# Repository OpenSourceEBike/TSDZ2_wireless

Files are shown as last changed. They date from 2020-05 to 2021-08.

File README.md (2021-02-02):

NEW UPDATED DOCUMENTATION HERE: https://opensourceebike.github.io/

https://opensourceebike.github.io/

# TSDZ2 Wireless

- Forum message: [Fully wireless ANT+ BLE TSDZ2 mid drive motor (like Specialized Turbo Levo) -- Flexible OpenSource firmware](https://endless-sphere.com/forums/viewtopic.php?t=106346)
- Developers: see [documentation](documentation/README.md)

We are also developing our own wireless remote although any other comercial wireless EBike remote will work: https://github.com/OpenSource-EBike-firmware/ebike_wireless_remote

TSDZ2 Wireless project aims
------------

This project aims to make TSDZ2 mid drive motor support wireless displays and wireless remote control buttons just like the new commercial ebikes as [Specialized Turbo Levo Ebike](https://www.youtube.com/watch?v=F43oqj1Zlww).

A very simple and cheap DIY board, that costs only 25€, will implement the wireless ANT+ LEV and Bluetooth. This board can be placed inside a small and waterproof black box, that will connect to the TSDZ2 motor display connector.

The wireless displays and wireless remote buttons are available from some different brands: Garmin, Wahoo, Sigma, O-synce, Specialized and Selfloops. Somes displays are simple with a monochrome screen and others are very advanced with GPS navigation, cycling fitness metrics and with wireless connection to cycling sensors like pedal power sensors and even tire pressure sensors.

The LCD Display will be replaced by the DIY board, a nRF52840 Bluetooth/ANT+ module and supporting circuitry. This allows the use of wireless buttons to control the TSDZ2 motor and it acts as a bridge between the motor, an Android phone running an app, and/or an ANT+ GPS/Fitness Display. It aims to be compatible with any display that can handle the ANT+ eBike data format, displaying relevant motor data and warnings. The Android app aims to duplicate (more or less) the 850C display, working either from the touchscreen or via wireless buttons on the handlebar.

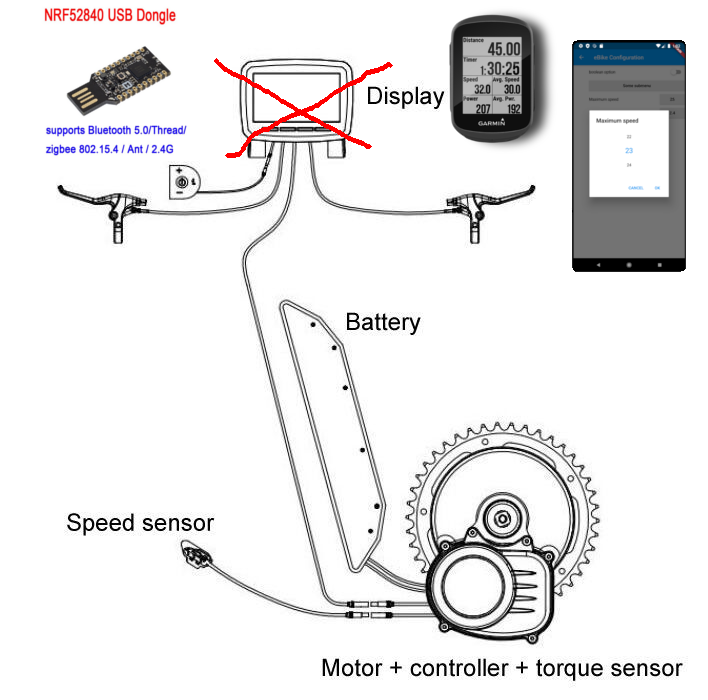
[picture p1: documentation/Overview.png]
Overview of connection


Warnings!
---------

1) Battery Voltage MUST!!!!!! be less than 60V otherwise smoke may escape.....
2) Spec. of DC-DC converter must be Input >60V and Output = 5V
3) Check output voltage of DC-DC converter BEFORE WIRING IT UP!!!

TSDZ2 cable pinout for LCD Display
----------------------------------
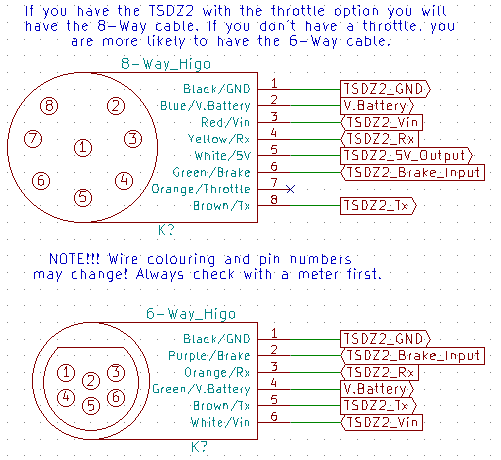
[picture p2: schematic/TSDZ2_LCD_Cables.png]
TSDZ2 Pinout for cables to standard LCD


The nRF52840 module needs to connect to the TSDZ2 motor-controller and the easiest way to do this is by either using an old LCD cable or buying an extension cable and cutting the relevant end off. The type of cable you have/need will depend on which TSDZ2 model you ordered - there are currently two types, one with a throttle and one without. The throttle needs a 5V connection as well as an anlogue input going to the motor-controller, so it has two extra cable - eight compared to the other motor-controller's six. For this project it is advised that you do not use the throttle, so either model is fine. The pinout of the two cable types is shown above - please note that the wire colouring and pin numbers may change! Always check with a meter first.

Connecting the nRF52840 UART to the TSDZ2 STM8S105 Motor-Controller UART
-------------------------------------------------------------------------------
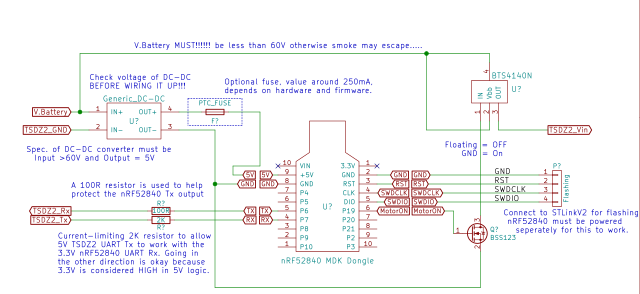
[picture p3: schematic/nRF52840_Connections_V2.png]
nRF52840 connections to peripherals


The TSDZ2 motor-controller's STM8S105 processor runs at 5V logic supply, whilst the nRF52840 processor runs at 3.3V. Unfortunately the nRF52 does not have 5V-tolerant GPIO inputs, so we need to be careful how we connect the two.

The nRF52 UART HIGH output (V.OH) is ~3.3V, which falls slightly out of the spec for the STM8S105 CMOS UART input, the datasheet for which states that 0.7xV.DD (3.5V) is expected for V.IH when run at 5V. However in practice it works reliably. So, as per the various 3.3V LCD displays, we can connect the nRF52 UART 3.3V output directly to the STM8S105 UART input, as shown above. For additional ESD safety we can add an optional low-value resistor to the nRF52 UART output.

Connecting the 5V STM8S105 UART output to the 3.3V nRF52 UART input is more problematic and there are [an almost infinite number of ways of doing this](https://next-hack.com/index.php/2017/09/15/how-to-interface-a-5v-output-to-a-3-3v-input/ "a random guide to interfacing 5v to 3.3v logic"). The easiest way is to rely on the [nRF52's input protection diodes](io_protection.png) to keep the input voltage below the maximum allowed.

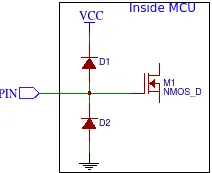
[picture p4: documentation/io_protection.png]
nRF52840 input protection diodes


If you just connect the two together a large amount of current will flow through the upper diode into the power supply, burning the diode out almost instantly and then destroying the input circuitry as the maximum voltage is exceeded. To avoid this, a current-limiting resistor is used as shown above. __NOTE__ - there is a trade off between small-resistor/high-current/high-speed and large-resistor/low-current/low-speed.

The absolute best way would be to use a pair of buffer/translators, [one with a TTL input running at 5V](https://www.ti.com/product/SN74AHCT1G125 "something similar to this") to drive the STM8S105 UART's input with a low-impedance output, and the other [with a CMOS input running at 3.3V](https://www.ti.com/product/SN74LVC1G34 "and something like this") to offer a high-impedance 5V-tolerant input to the STM8S105 UART's output. This offers the optimum noise resistance but at a higher cost and component count.

Connecting the nRF52840 to the STLinkV2 Programmer
--------------------------------------------------
For convenience it is advised that you permanently wire in a connector to allow programming the nRF52840, to allow for future Firmware updates - the pinout is up to you, as long as it matches the programmer's cable. Please note that the nRF52840 will need to be powered separately for the programming to be successful.

Connecting the nRF52840 to the BTS4140N High-Side Mosfet Relay
--------------------------------------------------------------
The high-side mosfet-relay input needs to be driven by an open-drain/open-collector circuit that can withstand the battery voltage across it when the device is floating. Following the BTS4140N datasheet on page 6, a BSS138 mosfet (supersedes BSS100) pulls the BTS4140N input to ground to make it conduct. When the mosfet is off, the BTS4140N stops conducting and the input floats at the battery voltage, which means that the Drain-Source breakdown voltage must be higher than 60V - the BSS138 is 100V.

Connecting power to the nRF52840
-------------------------------

A generic DC-DC converter is used to power the nRF52840's 5V input from the battery voltage. As such is should handle an input range of between 20V and 60V (check the capacitor ratings on the PCB) and provide a stable 5V supply at 1A. As mentioned above, connect it temporarily to your battery and check/adjust the output is correct before you start wiring up the nRF52840. When everything is connected up and running, it is worth checking it again and if it is adjustable, gluing the adjuster in place with a drop of nail-varnish - this has the right consistency to secure it against vibration but is easy enough to break the seal if you need to adjust it in the future. You can use a PTC fuse if you want - 250mA to 500mA is probably enough. Check it doesn't get warm/hot to the touch when in normal use - if it does, see how much voltage is being dropped across it and replace it with a larger value if it's more than 0.5Vish.
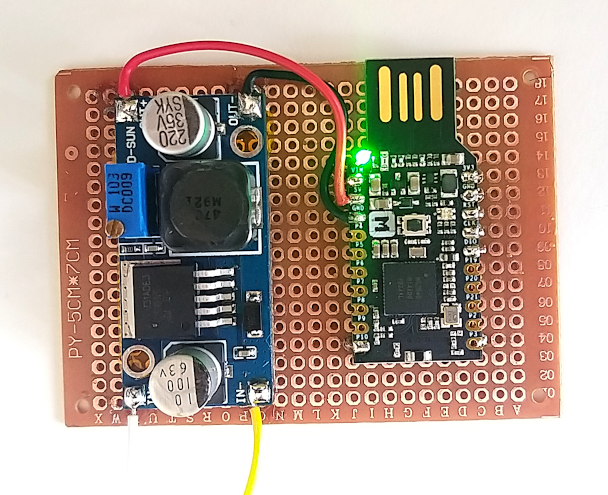
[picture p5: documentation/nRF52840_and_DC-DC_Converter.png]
Powering the nRF52840 with a DC-DC converter


Connecting brake sensors to the TSDZ2
-------------------------------------

It is strongly advised that you connect brake sensors/switches to the TSDZ2 motor-controller as it will increase safety of operation and reduce the chance of damage to the blue gear, in some circumstances. The brake input to the TSDZ2 is pulled up to 5V by a resistor inside the motor-controller, pulling the brake input to GND indicates that the brakes are being used. This is normally done with a switch (2-Pin Connector), but if you have the 8-Way Higo cable you can use a powered brake-sensor with three wires. In both cases the sensors need to be connected in parallel to the single TSDZ2 motor-controller brake input - check that any active sensors used have an open-collector output and are designed to be connected in parallel like this. The pinout and colour of the wires is likely to change without notice, so check first. An optional diode is shown, to protect from high voltages going into brake input. Use a Schottky type to reduce the dropped voltage when it's conducting. The optional Fuse is a PTC self-resetting type to protect the TSDZ2 5V supply - 50mA should be about right, but check the spec. of your 3-wire brake sensors first.

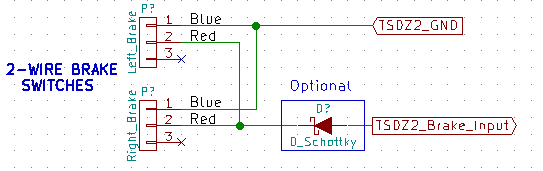
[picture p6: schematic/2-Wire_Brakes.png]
2-Wire brake connection


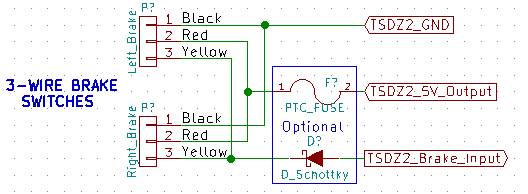
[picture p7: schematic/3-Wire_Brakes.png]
3-Wire brake connection


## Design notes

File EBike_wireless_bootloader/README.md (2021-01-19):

# TSDZ2 Bluetooth Bootloader

- Discussion Forum:[Fully wireless ANT+ BLE TSDZ2 mid drive motor (like Specialized Turbo Levo) -- Flexible OpenSource firmware](https://endless-sphere.com/forums/viewtopic.php?t=106346)
- Developers, see the [documentation](documentation/README.md)
- [We have also developed a wireless ebike controller for the TSDZ2 motor](https://github.com/OpenSource-EBike-firmware/TSDZ2_wireless)
as well as a [wireless remote control](https://github.com/OpenSource-EBike-firmware/ebike_wireless_remote); both use this bootloader.

-------
## Overview
This project implements a secure wireless bluetooth DFU bootloader for the TSDZ2 ebike remote control and motor controller. Once loaded on the Nordic Nrf52840 dongle, the firmware for both the remote and the wireless controller can be installed using bluetooth.

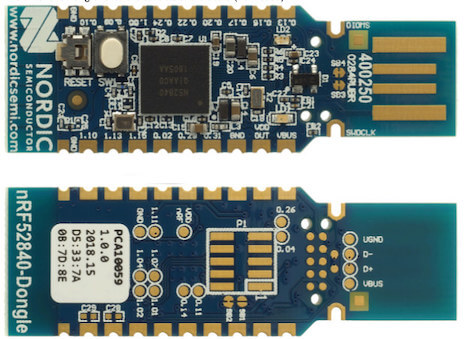
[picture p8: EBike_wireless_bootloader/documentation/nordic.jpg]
dongle


----
[Installing the Bootloader on the Nordic USB Dongle](documentation/getting_started.md)
-------
-------
[Loading New Firmware using the bootloader (the DFU Process)](documentation/dfu.md)
-----------
------------

[Technical Description](documentation/operation.md)
-----------
------------
[Security Encryption](documentation/configuration.md)
---------
---------
[Building the Bootloader](documentation/flashing.md)
------
------
[Bootloader Memory Map](documentation/memory_map.md)
-------
-------
[Important Note for Developers ](documentation/voltage_issue.md)
-------
-------
## Questions/Comments?
Please post on [this forum message](https://endless-sphere.com/forums/viewtopic.php?f=28&t=106346).

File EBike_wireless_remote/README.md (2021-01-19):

# EBike Handlebar Remote Controller

- Discussion Forum:[Fully wireless ANT+ BLE TSDZ2 mid drive motor (like Specialized Turbo Levo) -- Flexible OpenSource firmware](https://endless-sphere.com/forums/viewtopic.php?t=106346)
- Developers, see the [documentation](documentation/README.md)
- [We have also developed a wireless ebike controller for the TSDZ2 motor](https://github.com/OpenSource-EBike-firmware/TSDZ2_wireless)
as well as a [bootloader to be used with both the remote control and the ebike wireless controller](https://github.com/OpenSource-EBike-firmware/TSDZ2_wireless-bootloader)
## Overview
This project implements a wireless remote button for EBikes and/or GPS bike computers like the Garmin Edge. 
You can  purchase on the market ebike remote controls. ie: the [Garmin EBike Remote for about 80€](https://buy.garmin.com/en-US/US/p/545795/pn/010-12094-30).

However, our remote control is considerably less expensive and offers sevaral additional features for ebike control.

----
[Getting Started](documentation/getting_started.md)
-------
-------
[Operation](documentation/operation.md)
-----------
---
[ANT+ Control](documentation/features.md)
------------
------------
[Configuration Options](documentation/configuration.md)
---------
---------
[Battery considerations](documentation/battery.md)
-----
-----
[Further Development and Planned features](documentation/planned.md)
------
------

## Questions/Comments?
Please post on [this forum message](https://endless-sphere.com/forums/viewtopic.php?f=28&t=106346).

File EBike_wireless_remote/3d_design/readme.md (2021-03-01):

For 3D printing, use the files lower_part.stl and keypad.stl. Note that lower_part.stl seems to have non-manifold edges but I generated the GCode on Cura software and it printed well as if non-manifold edges are not an issue.

The other files are the sources files for the design on the FreeCAD 0.19 dev version. The assembly file has the assembly of the parts, including the NRF52 wireless board and the battery.

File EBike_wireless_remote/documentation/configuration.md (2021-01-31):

# Remote Configuration Options
The device configuration of the remote can be set via a bluetooth characteristic.

Once set, the configuration options are permanently stored in flash memory.
To change the remote configuration, long press the PLUS button to turn on bluetooth.
As an example of making a configuration change, see changing the ANT+ LEV Device Number (to connect to only one specific eBike) using the Nordic nRF Connect app in this video:

video (https://youtu.be/_ALauuDxZuQ) 

## The currently implemented configuration options are:
1. Setting the ANT+ Device number for the ANT LEV ebike. This ensures the remote will only pair to a specific ebike. valid inputs are hexadecimal 0x01 - 0x59 (decimal 01-89)
Please note that setting the device number to 0x00 is a 'wild card' setting that will cause the remote to pair with ANY ebike device number.
-----------------
2. __Turn on/off ANT+ LEV control.__ 
 (input hex 0x90 to turn on, hex 0x91 to turn off) 
This allows the remote to control only a garmin bike computer or any other device that implement the ANT+ Controls profile
----------
3. __Turn on/off ANT+ CONTROLS__  
 (input hex 0x92 to turn on, hex 0x93 to turn off)  
 This allows the remote to turn on/off the ANT+ CONTROLS capability depending on the use case. ie: the user may not have a garmin bike computer that needs to be controlled.
 --------
 4. __Turn on/off brake control__  depending on the use case
 (input hex 0x94 to turn on, hex 0x95 to turn off)  
 ---------
1. __Boot the remote control into Device Firmware Update (DFU) mode__ by inputting 0x99 to allow the remote firrmware to be updated wirelessly using bluetooth.
(input hex 0x99 to boot into DFU)  
---------
A video showing a DFU process can be seen here:
video (https://youtu.be/va3LJoiosoc) 
-------
## Display the current configuration
The currently selected configuration options can be displayed using the on board led by long pressing the ENTER button on the remote.
The LED will continue a visual cycle spanning 2 seconds when the button is held down as follows:

- __RED LED__ (0n for 0.5 seconds) - ANT+ LEV active
- __GREEN LED__ (0n for 0.5 seconds) - ANT+ CONTROLS active
- __ALL LEDs OFF__ for 0.5 seconds
- (__repeat__ while button is pressed)

## [back](../README.md)

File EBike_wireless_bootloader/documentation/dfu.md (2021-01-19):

# The Device Firmware Update (DFU) Process
The DFU process can be run by using one of the following Nordic tools. Each of these tools is used to send the DFU package to the target device to perform the update.

* The nrfutil command-line tool
* nRF Connect for desktop
* nRF Connect for mobile
Two devices are involved in the DFU process: the DFU controller which transfers the DFU package, and the DFU target which receives and applies the DFU package. (the TSDZ2 remote or controller)

---------
Step 1. Generate DFU .zip packet
--------
--------
A DFU .zip packet is required for the DFU master to send new image(s) to the TSDZ2 remote control or controller boards.(the target) The .zip file contains the image hex file(s) we want to update and the init packet, including the signature of the packet. 
Prepare the TSDZ2 application zip file. Build the TSDZ2 remote control and/or the TSDZ2 controller and find the .zip file inside the _build folder. It's named TSDZ2_combined_with_sd. 
The make file uses nrfutil to generate the packet zip file.
The syntax is as follows:
nrfutil pkg generate --hw-version 52 --application-version 1 --application nrf52832_xxaa.hex --sd-req 0x98 --key-file private.key app_dfu_package.zip
Explanation:
--hw-version: This should match the chip on the dongle. We use the nRF52840 SOC chip, hence "52". 
--application-version: By default the start number for the application version is 0.  
--sd-req: For the TSDZ2, we need Softdevice S340 v6.1.1. The number to use for this softdevice version is 0xB9. 
--application : Tells nrfutil that you going to update the application and an application image is provided.

----------
Step 2. Performing DFU (Bluetooth)
--------
---------
Now you have your DFU .zip file containing the application update and the bootloader and bootloader settings installed on the board, it's time to actually do wireless DFU.
1.  Start DFU mode
     This can be done by entering 0x99 as a configuration variable in either the remote control or wireless controller firmware using bluetooth control.
     You can also initiate DFU mode by holding the board button down for several seconds during a reset. (ie: when power cycling, or pressing the reset button on the board)
   
     Verify the bootloader starts advertising as "TSDZ2_DFU".You’ll need to make sure the package you created in step #7 is accessible on the mobile phone you’re using (if you’re using nRF Connect for Mobile). Now, connect to the DFU target:

2. Copy the DFU .zip file you just generated to the phone or to the folder on PC of your choice.
   
3. Use nRFConnect/nRFToolbox app either on the phone or on PC to connect and do an OTA DFU using the .zip file you copied (Press DFU button).After you’ve connected to the DFU target in nRF Connect on Mobile, swipe to the left twice to navigate to the DFU screen. Then click “Open Document Picker”:Choose the .zip file  and start the DFU process.
Click the “Start” button:
   
4. Once the DFU process is complete, you should see that your new application (that was part of the DFU package) is now running on the DFU Target 

Here is a video showing a wireless DFU for the TZDZ2 remote control:
video (https://youtu.be/va3LJoiosoc)

## [back](../README.md)

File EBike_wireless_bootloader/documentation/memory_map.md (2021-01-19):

# Firmware memory map
See this video for an explanation of the memory map for the nRF52840 board:
video (https://youtu.be/MZ6Qz32tY0c)  
## [back](../README.md)

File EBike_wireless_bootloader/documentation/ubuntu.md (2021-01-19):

# Flashing with Ubuntu
1.    Open a terminal
2. Install OpenOCD (to connect to STLinkV2):
   
   Enter: __sudo apt-get install openocd__:

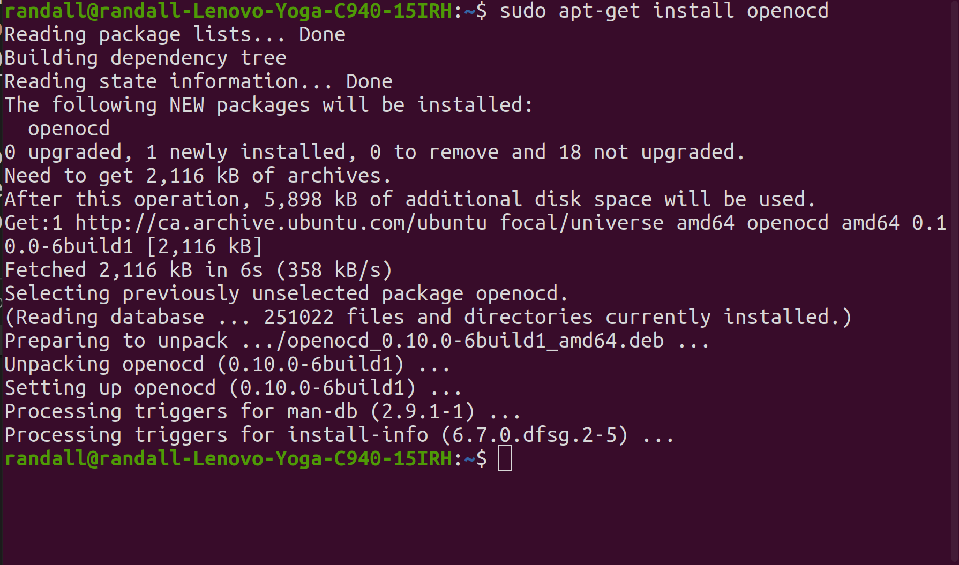
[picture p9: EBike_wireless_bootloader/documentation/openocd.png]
   
 
3. Connect the STLinkV2 to the board. For the  nRF52840 Nordic Dongle see the pinout below to connect to the SWDIO, SWDCLK, and GND pins, note that you do not need to connect the RST pin.
   
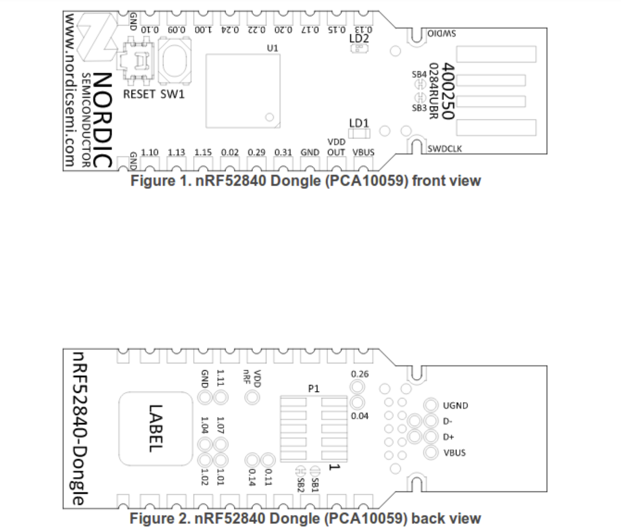
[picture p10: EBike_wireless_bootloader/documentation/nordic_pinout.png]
   

4. Note that you will also need to install the STLinkV2 udev rules file that are on the firmware/tools/ folder, so the STLinkV2 can be accessed by the OpenOCD:
    ```
    sudo cp 60-st_link_v2.rules /etc/udev/rules.d
    sudo udevadm control --reload-rules
    ```

5. From the terminal window, navigate to the openocd directory, and enter the following command to start the openocd server:

NOTE: donwload the bootloader HEX file from here: https://github.com/OpenSourceEBike/TSDZ2_wireless-bootloader/releases
   
    ```
    $ openocd -f stlink-v2.cfg -f nrf52.cfg
    ```  
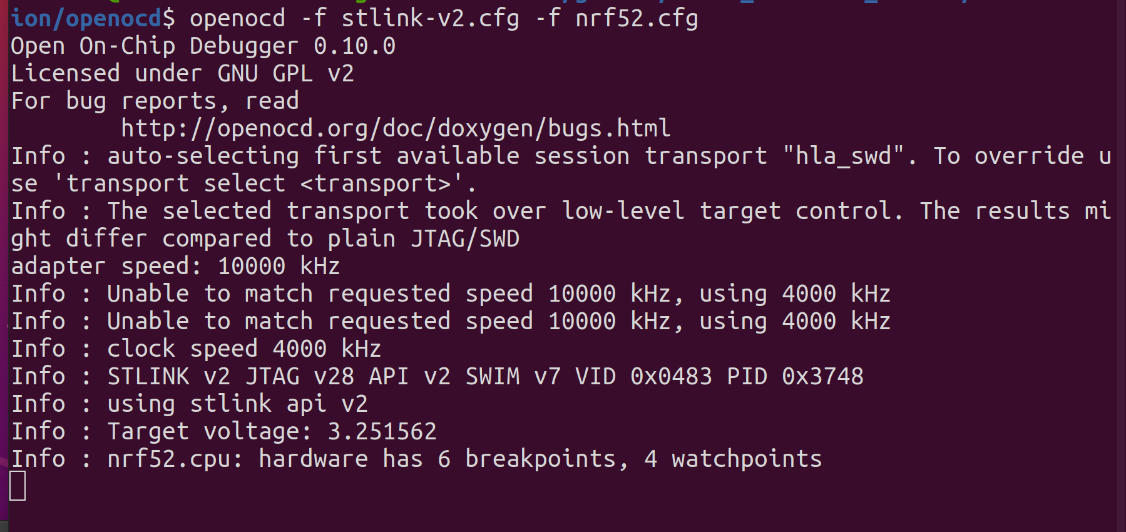
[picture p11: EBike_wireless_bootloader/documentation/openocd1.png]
    

6. Start another terminal session to access the openocd server, and enter the following command:
    ```
    $ telnet localhost 4444
    $ reset init
    $ halt
    $ nrf5 mass_erase
    $ program (path to hex)/TSDZ2_bootloader_with_sd.hex verify
    $ reset exit 
    ```  

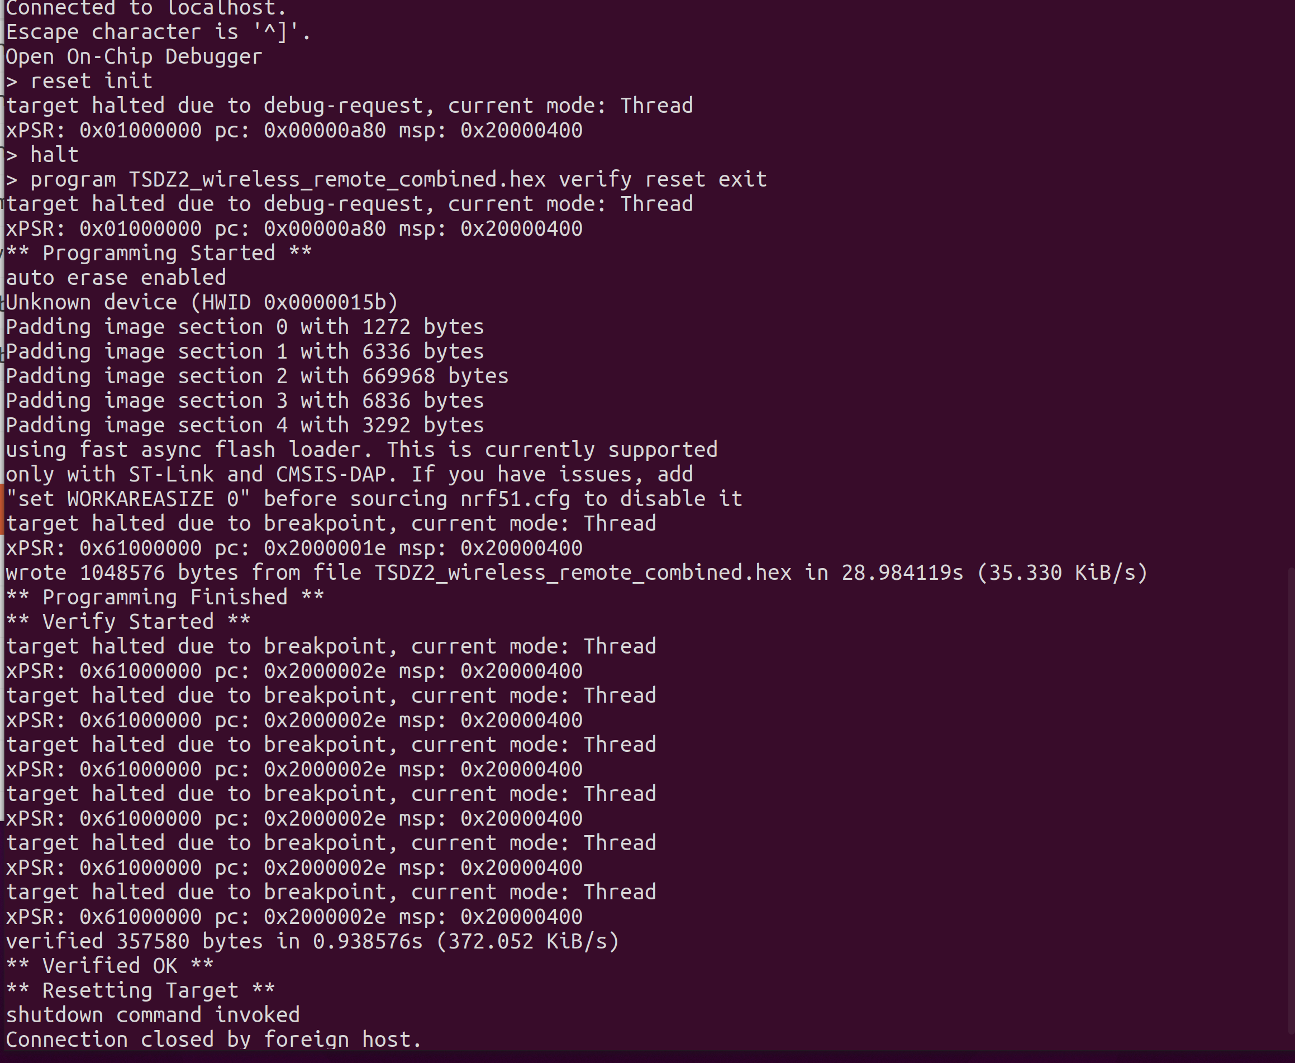
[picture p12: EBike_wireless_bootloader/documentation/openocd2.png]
    

This will flash and verify the write.
If you see ** Verified OK **, the flashing has been successful.

Congratulations!
-------
* You now have the bootloader installed on the Nordic board.
* Future firmware upgrades can be done wirelessly.
* For more information on how to use the bootloader's Device Firmware Update (DFU) process to install a bootloader update or the remote control firmware or the wireless controller firmware, see [Understanding The Bootloader DFU Process](../documentation/dfu.md).

## [back](getting_started.md)

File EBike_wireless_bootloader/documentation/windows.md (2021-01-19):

# Flashing with Windows

1. Install [openocd for windows](https://gnutoolchains.com/arm-eabi/openocd/)
2. You can now flash the firmware by following the openocd instructions located [in step 5](ubuntu.md)

## [back](getting_started.md)

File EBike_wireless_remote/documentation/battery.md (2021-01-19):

# Battery considerations
* To preserve the battery life, bluetooth should only be on when configuring the remote. If you forget to turn it off, the remote will disable bluetooth in 5 minutes
* The remote will go into ultra low power mode if it fails to connect to a device within ~30 seconds, or if no buttons are pressed for 1 hour. The system wakes up from ultra low power when the user presses any button.
* It is expected that a coin cell will be able to power the remote for one bicycle season. (6-12 months) 
* replace the battery annually. [Click here for a detailed study of the power modes of the remote and a battery life estimation](./Power_Analysis.md)
  The green is approximately approximately twice the lumen outpur of the red and blue leds for the same current! This can be seen in the following chart where the light output for the various leds was measured as a function of current and duty cycle.

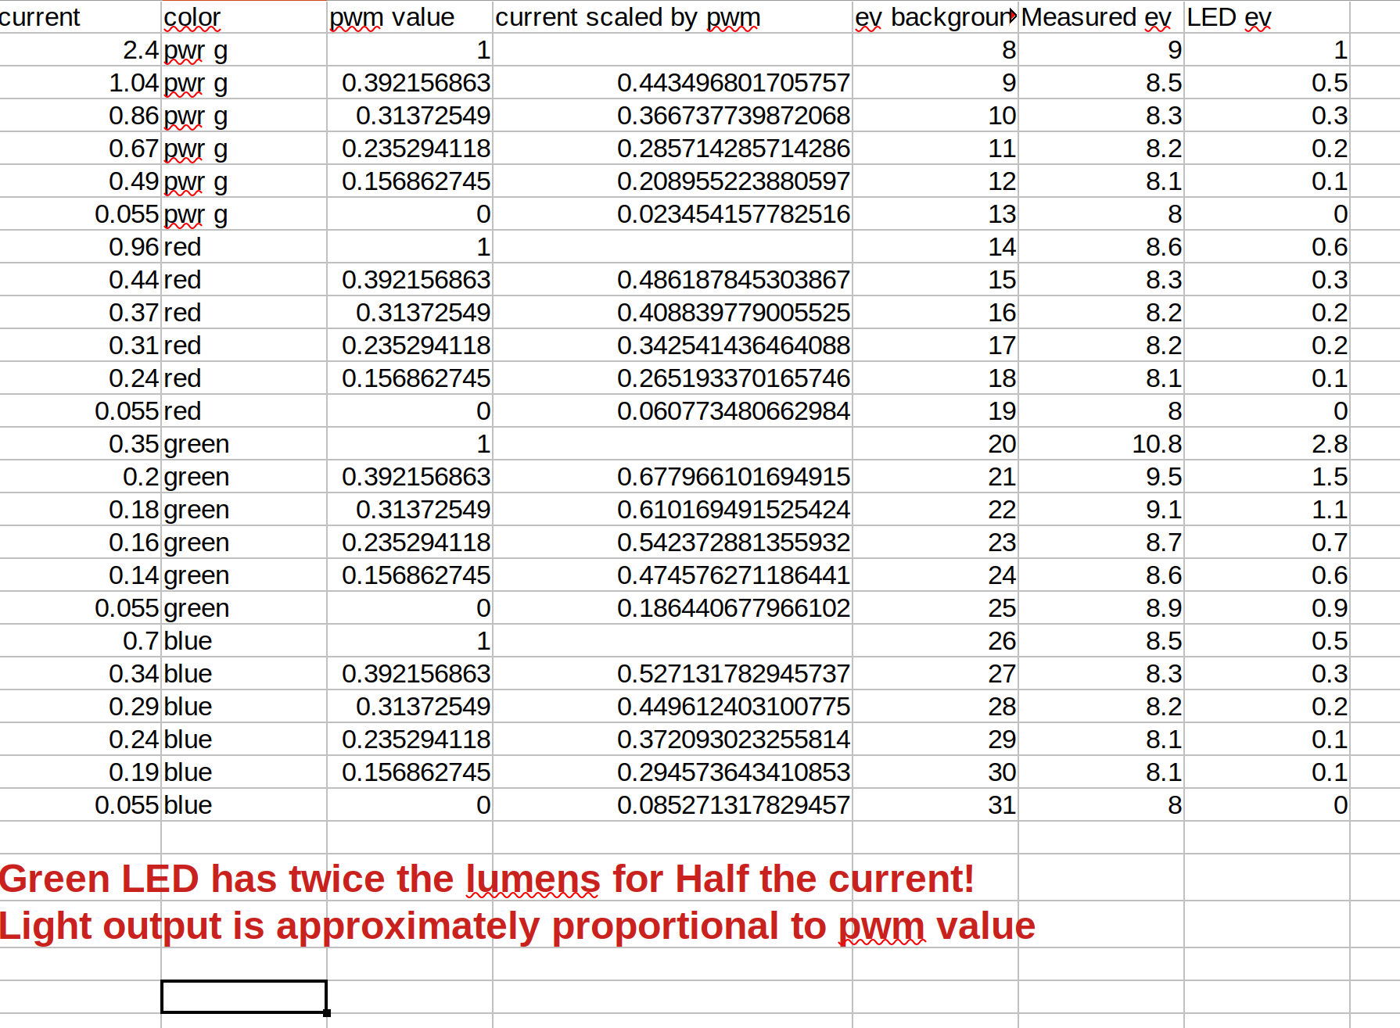
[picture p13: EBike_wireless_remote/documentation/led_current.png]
  
  ## [back](../README.md)

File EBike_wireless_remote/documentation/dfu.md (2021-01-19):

# The Device Firmware Update (DFU) Process
The DFU process can be run by using one of the following Nordic tools. Each of these tools is used to send the DFU package to the target device to perform the update.

* The nrfutil command-line tool
* nRF Connect for desktop
* nRF Connect for mobile
Two devices are involved in the DFU process: the DFU controller which transfers the DFU package, and the DFU target which receives and applies the DFU package. (the TSDZ2 remote or controller)
----
DFU Procedure
------
-----
1.  **Start DFU mode**
     This can be done by entering 0x99 as a configuration variable in either the remote control or wireless controller firmware using bluetooth control.
     You can also initiate DFU mode by holding the board button down for several seconds during a reset. (ie: when power cycling, or pressing the reset button on the board)
   
     Verify the bootloader starts advertising as "TSDZ2_DFU".You’ll need to make sure the package you created in step #7 is accessible on the mobile phone you’re using (if you’re using nRF Connect for Mobile). Now, connect to the DFU target:

2. **Copy the DFU .zip file for the wireless remote to the phone or to the folder on PC of your choice** 
     This can be done by simply emailing the update file to your device.
   
3. **Use nRFConnect/nRFToolbox app either on the phone or on PC to connect and do an OTA DFU using the .zip file you copied** 
     To start the process, press the DFU button. Then click “Open Document Picker”Choose the .zip file  
4. **Click the “Start” button** 
     The DFU will begin
   
5. **the DFU process is now complete** 
   Once the DFU process has completed, you should see that your new application (that was part of the DFU package) is now running.

Here is a video showing a wireless DFU for the TZDZ2 remote control:
video (https://youtu.be/va3LJoiosoc)

## [back](getting_started.md)

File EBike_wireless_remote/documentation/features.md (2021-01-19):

# ANT+ Control Features
This wireless remote button implements two ANT+ profiles:
1. the __ANT+ CTRL profile__ allowing it to control the page view on compatible bike computers - see the user manual of your device to see if it supports this profile. The remote will pair with any device that supports this profile. Typically, garmin bike computers support this profile for page control.
   
2. __The ANT+ LEV__ (Light Electric Vehicle) profile allowing the remote to control various features of the eBike including  changing the assist level. 
The remote will work with any eBike that support the ANT+ LEV profile. Of course, the TSDZ2 wireless eBike controller supports the ANT+ LEV profile.
see: [wireless EBike TSDZ2](https://github.com/OpenSource-EBike-firmware/TSDZ2_wireless) for more information.

## [back](../README.md)

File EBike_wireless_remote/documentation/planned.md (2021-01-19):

# Further Developments and Planned Features

  * Other possible ANT+ button assignments:
    * ie: Light control
    * Turn signal indication
    * Throttle Control of the TSDZ2 motor
  * Low battery  indication
  * Design a suitable housing for the board and battery.
  For this, two options are currently being considered:
    1. __The design of a suitable spacer for 3D printing that can reuse the VLCD5 keypad and handlebar connector__ (basically, the top and bottom portions of the keypad)  Inital design attempts are located in the 3d_design folder. 
    2. __The design of a seperate housing for the board + coin battery__. This has the advantage of allowing the board LED to be visible and the possible use of a larger battery for even longer life.
   No design efforts have started on this option. If you would like to contribute to this effort, please let us know in the [forum](https://endless-sphere.com/forums/viewtopic.php?t=106346).

## [back](../README.md)

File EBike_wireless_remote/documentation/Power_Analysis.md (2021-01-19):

# Remote Control Power Analysis 
A very useful tool for determining power utilization of nrf52840 boards is the [Nordic Power Profile Kit](https://www.nordicsemi.com/Software-and-tools/Development-Tools/Power-Profiler-Kit-2)
This tool was used with the remote control to estimate the useful lifetime of a CR2032 coin battery used with the remote control.
## Setup
The remote control was powered on the VDD pin with a 3V CR3032 lithium battery following the instructions described in [Getting started -Convert the board to use an external coin battery](./getting_started.md)
## Remote Control Power modes 
The firmware for the remote control has two low power operating modes.
1. **POWER IDLE MODE** This is the default power mode of the remote when it is not processing any button commands.
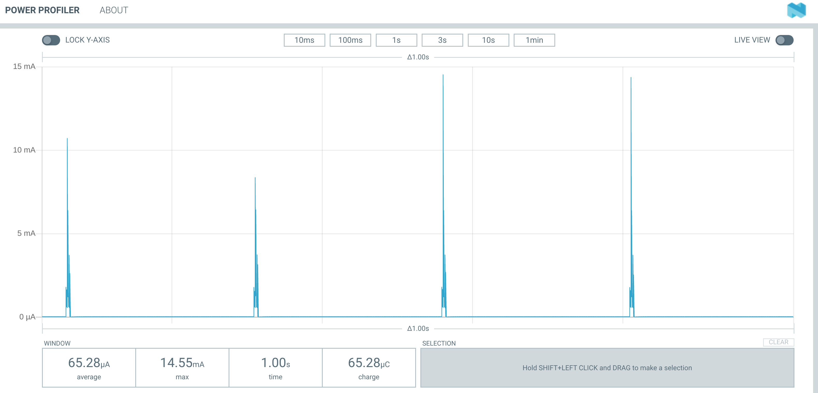
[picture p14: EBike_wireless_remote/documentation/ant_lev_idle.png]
The average current dissipated by the remote in this mode with Ant Lev active is 65.28uA as shown below:
The spikes in the current is caused by the switching voltage regulator used in the nrf52840 board. Essentially, the board power supply uses capacitive charging/discharging to reduce power consumption, and this leads to spiking in the current. 
If both Ant Lev and Ant Controls is active in the remote the average idle current jumps to 88.69 uA as shown below:
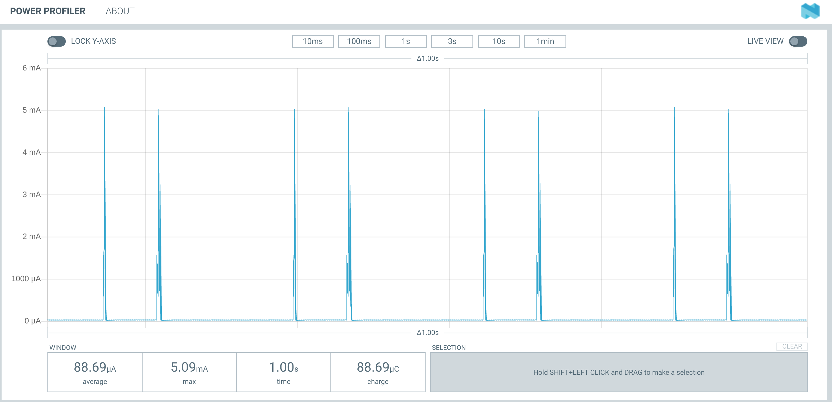
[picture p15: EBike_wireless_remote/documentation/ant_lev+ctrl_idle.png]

In **POWER IDLE** mode, the remote is powered on and ready to immediately process button commands.
2. **POWER OFF MODE**
   In this mode, the remote control turns off all  bluetooth and ANT wireless capabilities. The remote is put into a minimal power dissipation mode. The average power off current in this mode is only 0.44 uA as shown below:
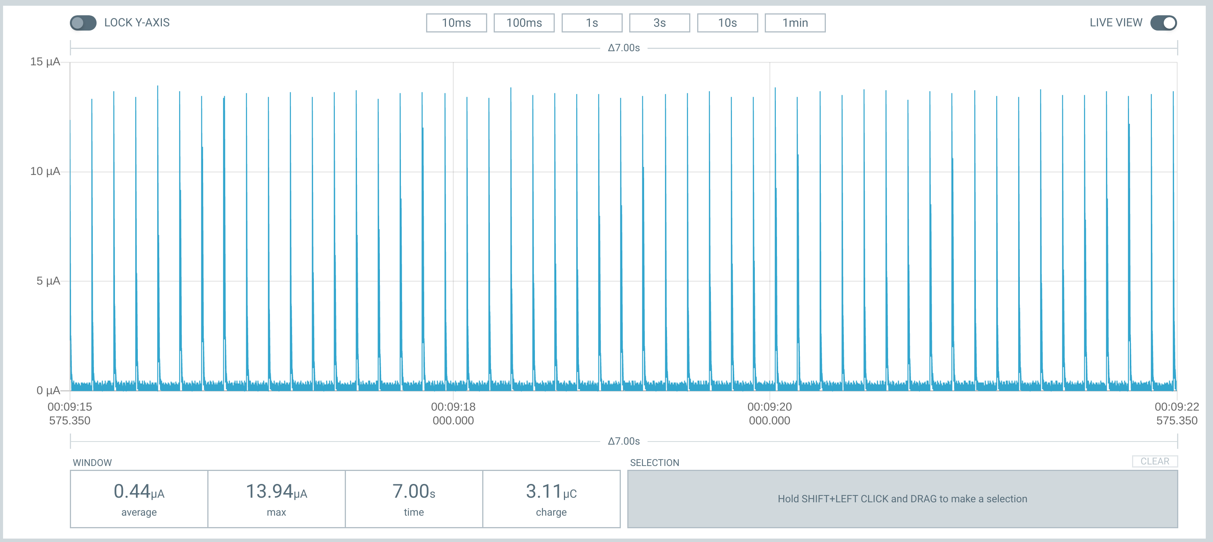
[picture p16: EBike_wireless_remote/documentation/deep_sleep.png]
   
3. **ANT LEV TRANSMISSION MODE**
    In this mode, either the plus or minus button is pressed to increase or decrease the assist level on the ebike.
    The average current dissipated by the the remote control when the remote control is pressed once a second is 101uA as shown below:
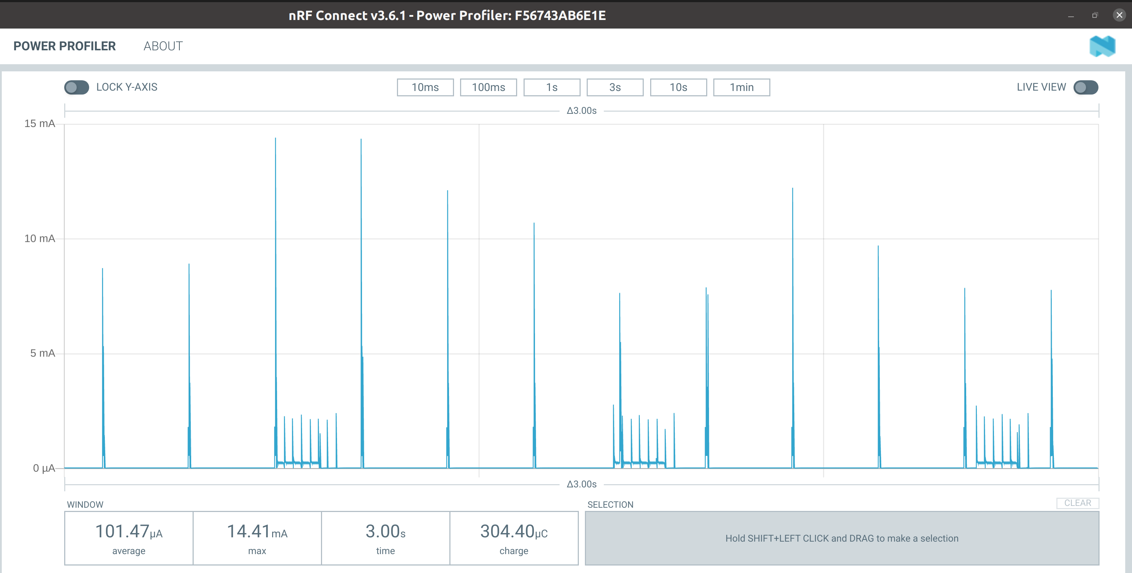
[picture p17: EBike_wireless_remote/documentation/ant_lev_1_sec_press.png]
    
    if the button is pressed once every 2 seconds, the average current drops to 90.5uA, as shown below:
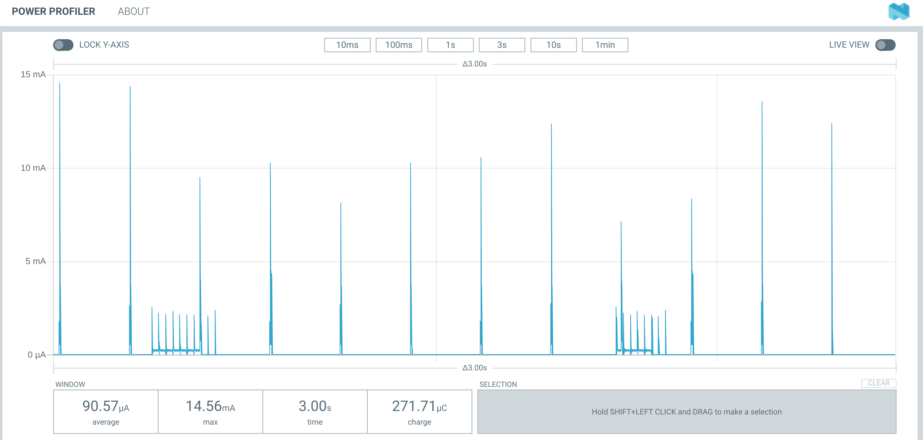
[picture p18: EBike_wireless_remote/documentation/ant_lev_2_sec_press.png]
    
4. **ANT LEV + ANT CONTROLS TRANSMISSION MODE**
   In this mode, both Ant Lev and Ant Controls are active. The average current is 140uA when the plus button is pressed once every second as shown below:
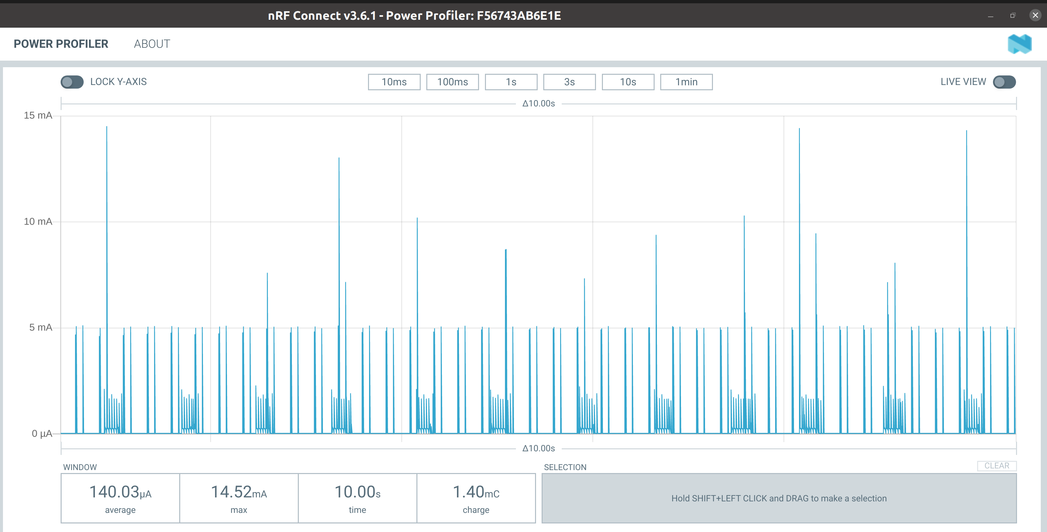
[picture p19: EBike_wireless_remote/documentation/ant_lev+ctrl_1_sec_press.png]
   
   if the plus button is pressed once every 2 seconds, the average current drops to 109.2 uA, as shown below:
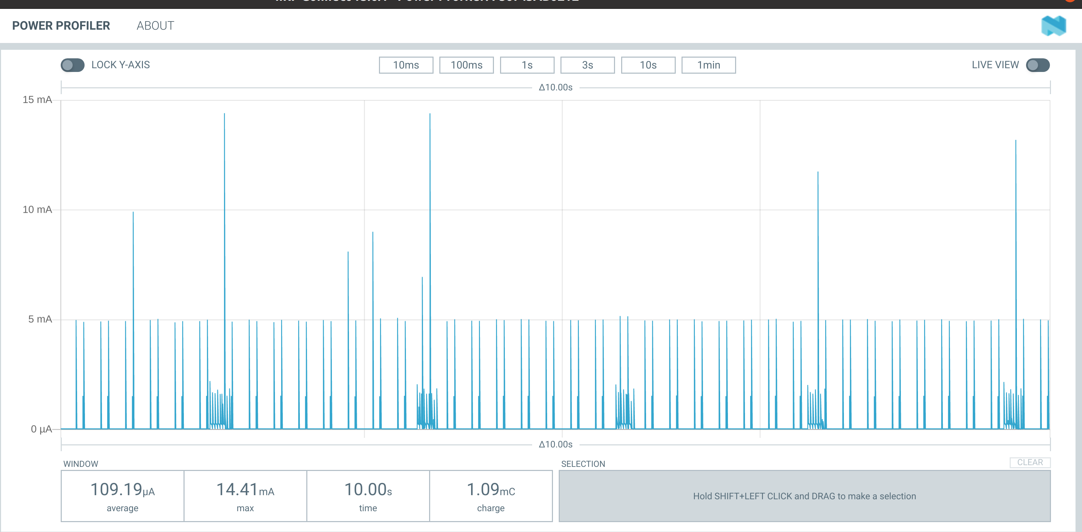
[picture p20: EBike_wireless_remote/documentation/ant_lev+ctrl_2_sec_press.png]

5. **ANT PAIRING MODE**
   When the board is searching for an ANT device, the average current dissipated by the board is 1 mA, as shown below:
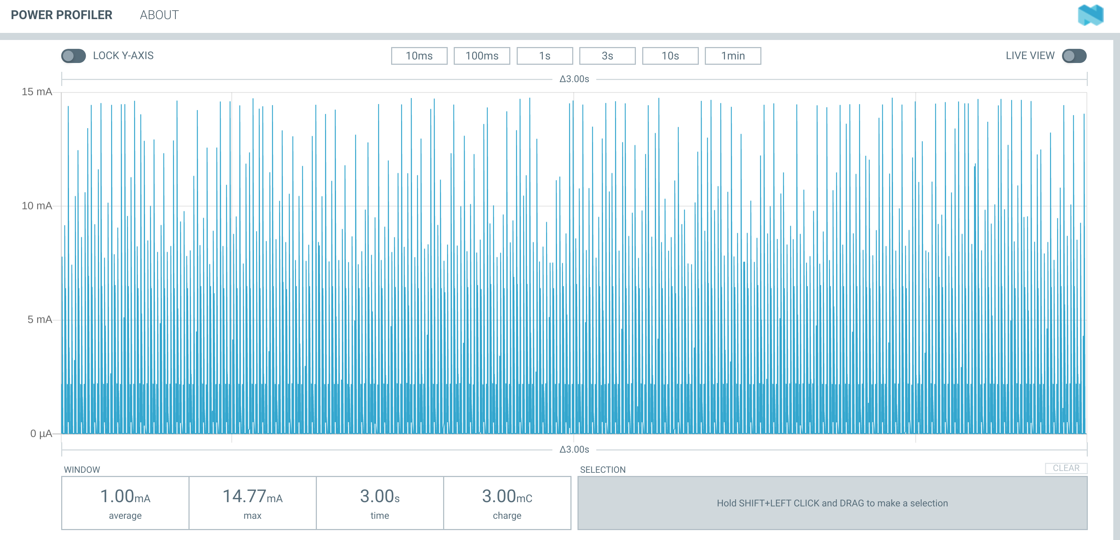
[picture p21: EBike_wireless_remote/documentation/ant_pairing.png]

6. **BLUETOOTH PAIRING MODE**
 When the board is searching for an Bluetooth device, the average current dissipated by the board is 375.82 uA, as shown below:
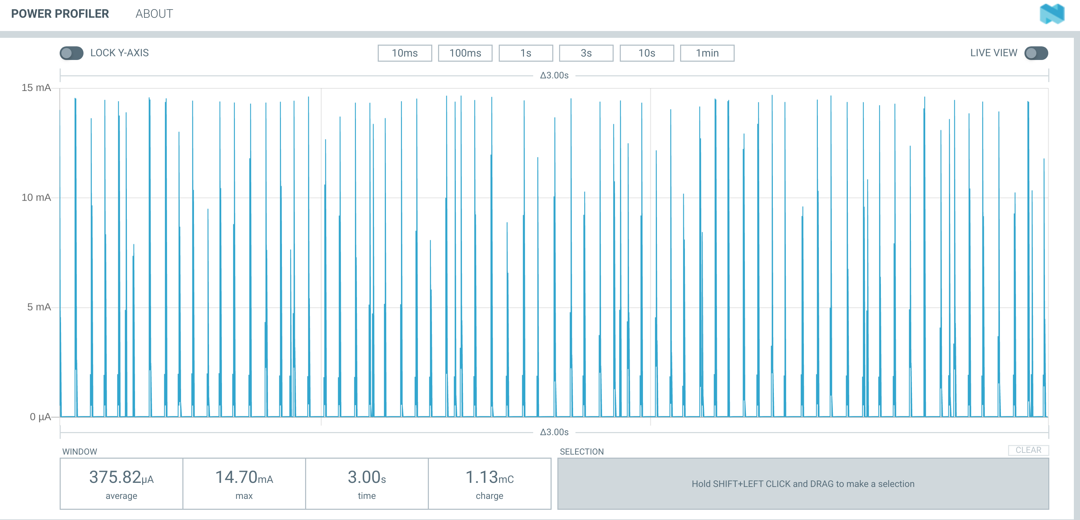
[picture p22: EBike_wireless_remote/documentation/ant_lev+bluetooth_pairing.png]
 
 7. **BLUETOOTH PAIRED MODE**
   In this mode the board is paired with a bluetooth device and is exchanging data. In this case, the average current is 137.2uA as shown below:
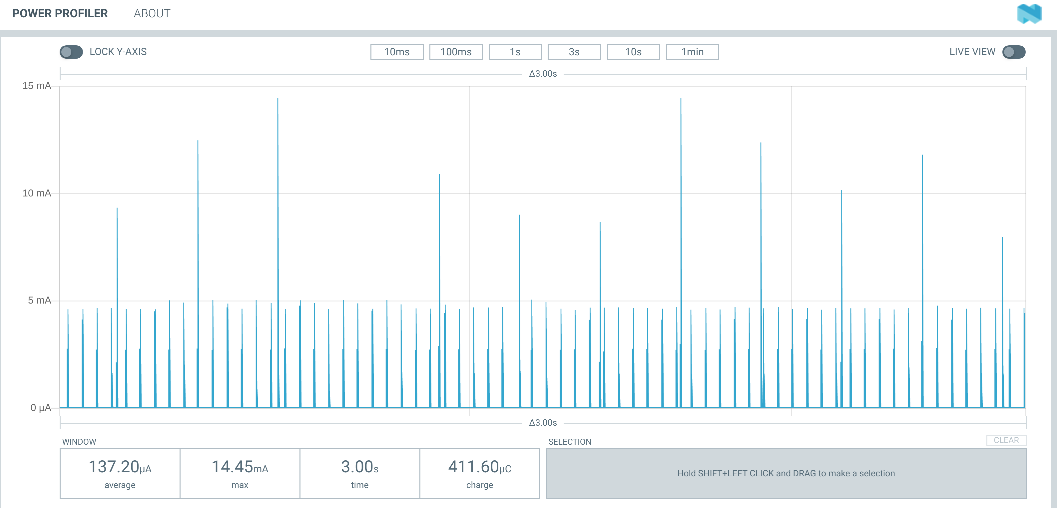
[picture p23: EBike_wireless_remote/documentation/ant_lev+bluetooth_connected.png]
   
 8. **BLUETOOTH IDLE MODE**
   In this mode, bluetooth is connected, but no data is being exchanged. The average current is  75 uA, as shown below:
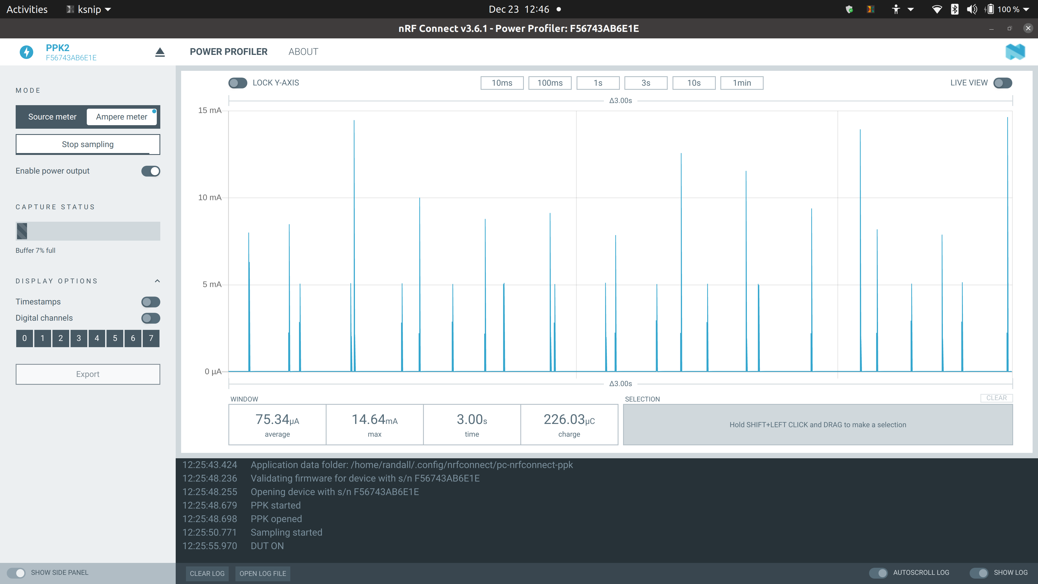
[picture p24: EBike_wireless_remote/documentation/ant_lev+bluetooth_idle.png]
   
 9. **LEDS ON MODE**
   In this mode either the RED, GREEN, or BLUE LEDS are active. The average LED current when on is 4.6ma (RED), 4.0ma (GREEN) and 4.1ma (BLUE) as can be seen below when the [ENTER] button is long pressed:
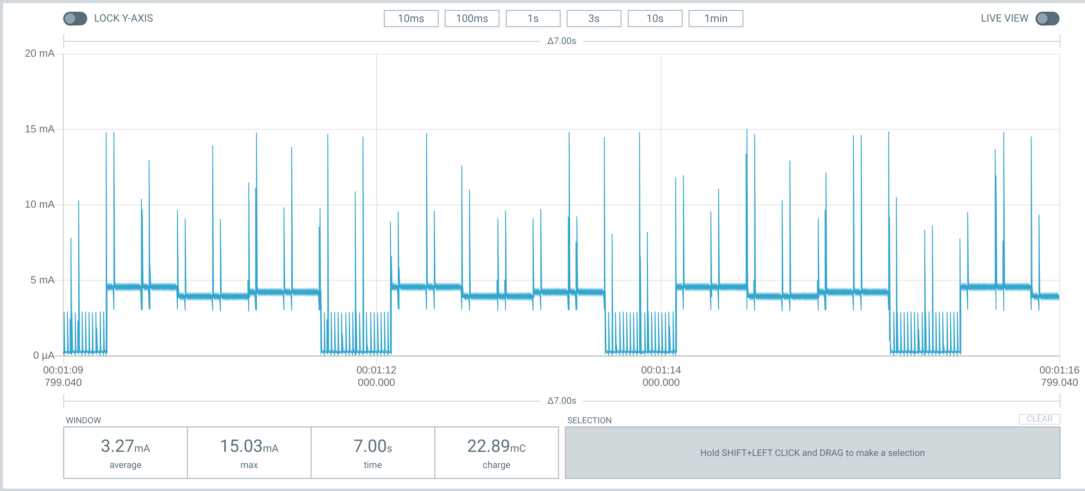
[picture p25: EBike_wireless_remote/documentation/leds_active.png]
   
   Obviously, LED utilization should be kept to a minimum to reduce battery drain on the coin cell.

   ## CR2032 Battery life estimation
   To estimate the battery life of this battery, we use this [spreadsheet](./Battery_Life_Calculator.xls), along with some conservative assumptions:

   - The milliamp-hr (mah) energy capacity of the CR2032 battery is rated at 225mah, conservatively de-rated to 80% or 180 mah based on [an analysis done by Nordic Semiconductor on the impact that switching power supplies have on the performance of a CR2032 coin cell](./High_pulse_drain_impact_on_CR2032_coin_cell_battery_capacity.pdf) 
  The conclusion of this document is shown below:
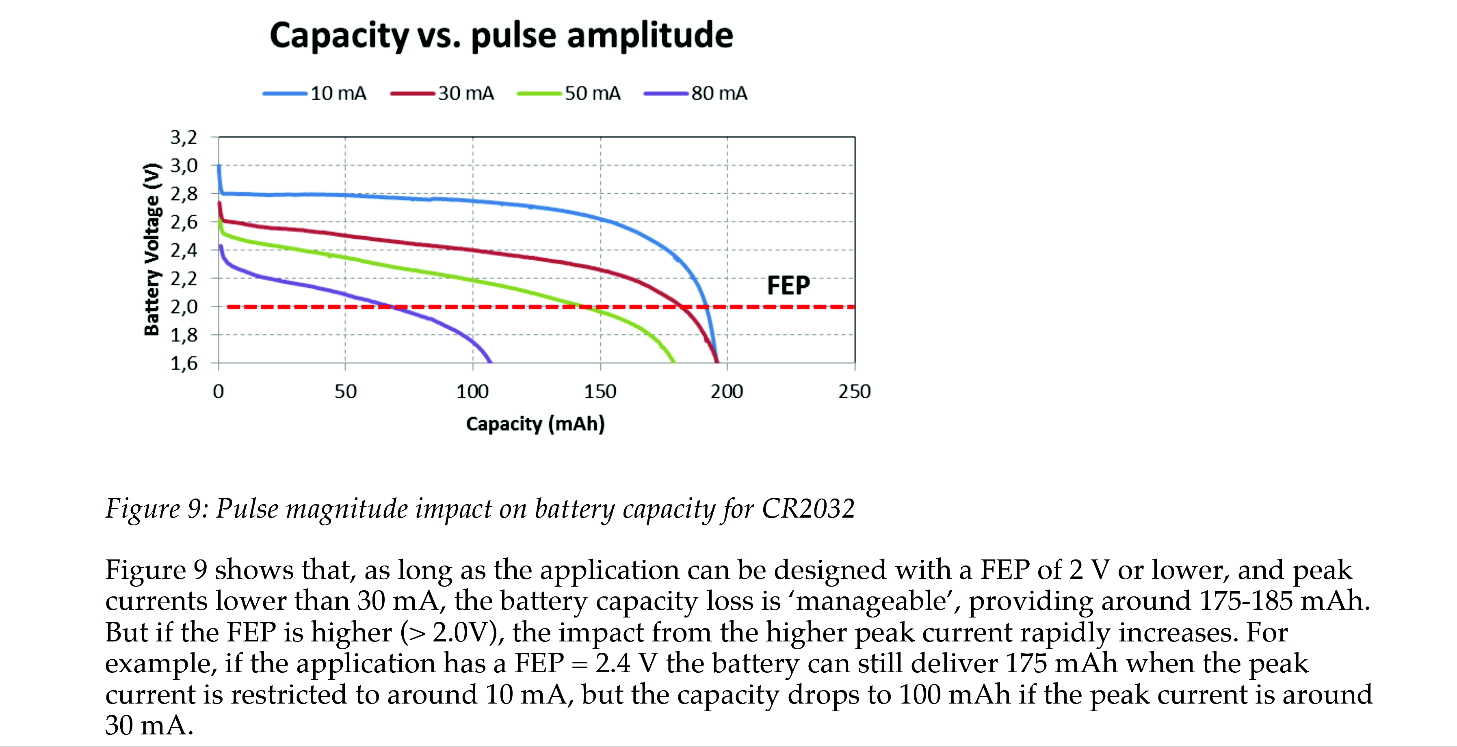
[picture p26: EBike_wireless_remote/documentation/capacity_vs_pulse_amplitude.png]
  
  FEP is the "Functional End Point" voltage at which the remote will no longer operate. (2 V). As can be seen from the power mode graphs above, the current peaks in the remote are between 10 and 15ma. We can therefore expect approximately 180 mah effective capacity from a CR2032 cell.
  This is the battery capacity used in the estimation of battery life.
   - The idle current is 66uA (see **POWER OFF MODE** above)
   - the **POWER OFF** current is 0.6 uA
   - The wake current is 100 uA (see **ANT LEV TRANSMISSION MODE** above)
   
   - the average duration of a button click (where the board is in transmitting mode) is 58ms as measured below:
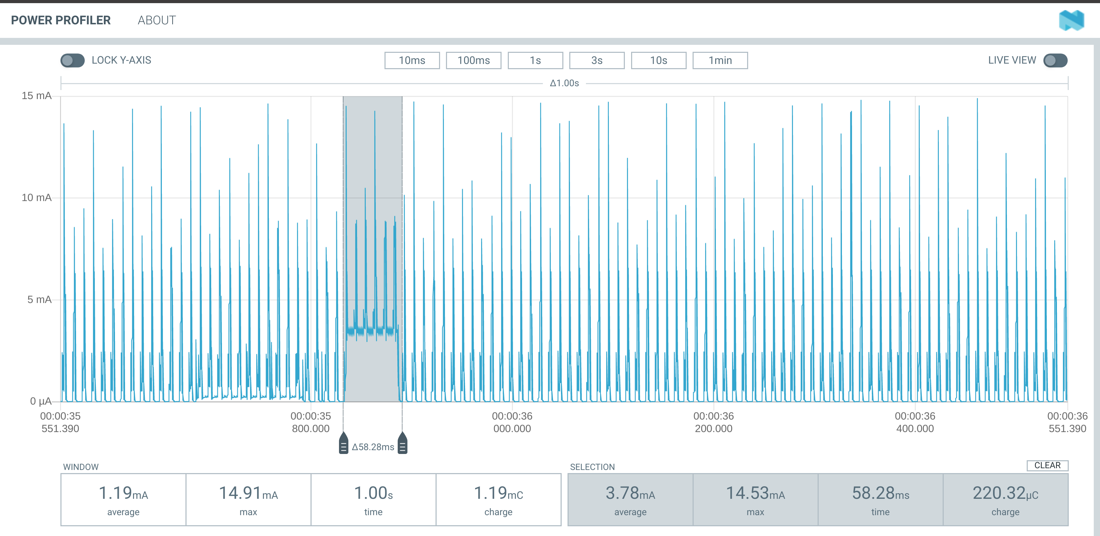
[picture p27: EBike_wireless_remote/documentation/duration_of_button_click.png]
  
   -  The ebike is ridden 18hrs/week
   -  The remote control spends virtually no time in bluetooth mode. (bluetooth is used only when setting up the remote)
   - The Leds are used sparingly
  Feeding these assumptions into the  [Battery Life Calculator](./Battery_Life_Calculator.xls) spreadsheet, the battery life is estimated to be **29 months!**. 
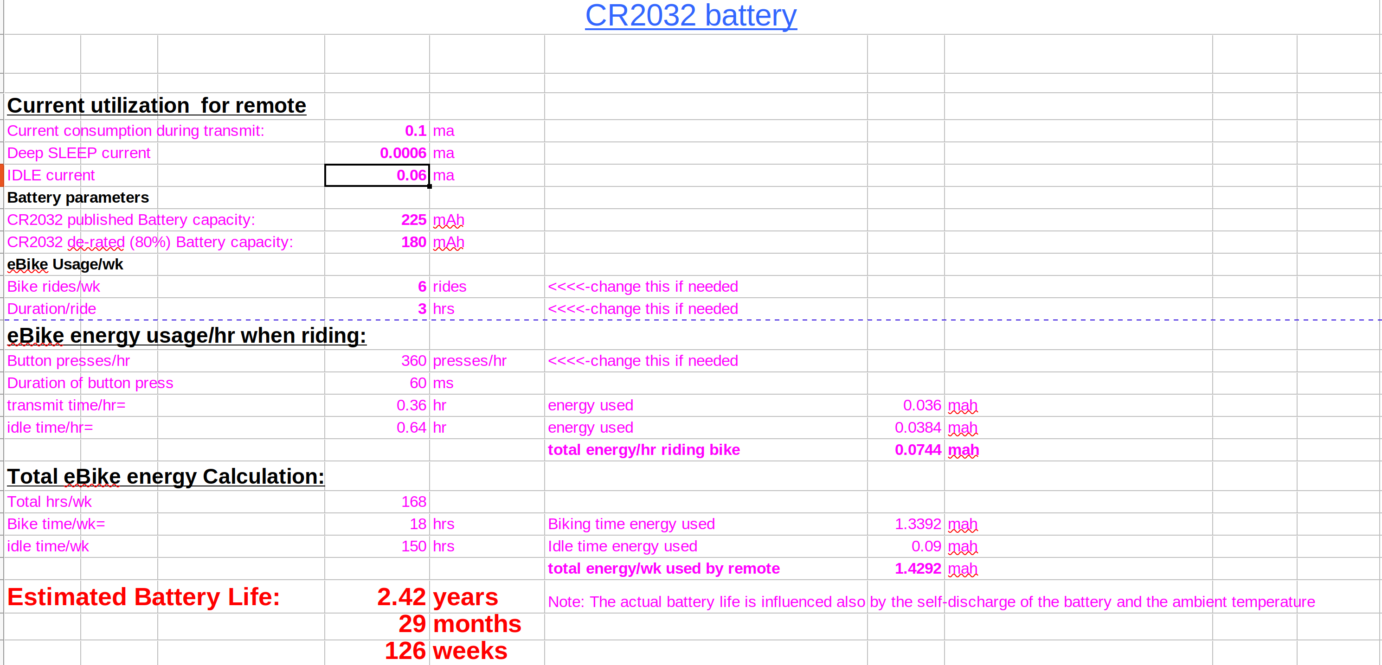
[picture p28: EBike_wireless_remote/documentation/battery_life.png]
  
  ## Conclusion
  Based on quite conservative assumptions, it is expected that the remote will continue functioning well for at least a year. 
  **Replacing the battery annually is recommended.**
## [back](./battery.md)

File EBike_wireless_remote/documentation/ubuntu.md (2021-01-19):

# Flashing with Ubuntu
1.    Open a terminal
2. Install OpenOCD (to connect to STLinkV2):
   
   Enter: __sudo apt-get install openocd__:

   
 
3. Connect the STLinkV2 to the board. For the  nRF52840 MDK Dongle see the pinout below to connect to the SWD pins, note that you do not need to connect the RST pin.
   
   

4. Note that you will also need to install the STLinkV2 udev rules file that are on the firmware/tools/ folder, so the STLinkV2 can be accessed by the OpenOCD:
    ```
    sudo cp 60-st_link_v2.rules /etc/udev/rules.d
    sudo udevadm control --reload-rules
    ```

5. From the terminal window, navigate to the openocd directory, and enter the following command to start the openocd server:
   
    ```
    $ openocd -f stlink-v2.cfg -f nrf52.cfg
    ```  
    

6. Start another terminal session to access the openocd server, and enter the following command:
    ```
    $ telnet localhost 4444
    $ reset init
    $ halt
    $ program (path to hex)/TSDZ2_wireless_remote_combined.hex verify reset exit   TSDZ2_wireless_remote_combined.hex 
    ```  

    

This will flash and verify the write.
If you see ** Verified OK **, the flashing has been successful.

Congratulations!
-------
You now have the board programmed.

Future firmware upgrades can be done wirelessly.
  
## [back](getting_started.md)

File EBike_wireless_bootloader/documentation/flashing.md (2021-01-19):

# Building the Bootloader
## The Garmin S340 softdevice
This bootloader (as well as the TSDZ2 remote control and controller firmwares) require the Garmin S340 softdevice to gain access to the bluetooth stack. Because of this, the S340 softdevice hex file needs to be flashed along with the bootloader hex file. The MAKE file will automatically combine these two hex files and flash the resulting combined file to the board. 
## Release Binary Hex file
If you're just looking to flash the combined bootloader and softdevice, simply flash this hex file using OPENOCD from the launch json menu in vscode for the respective giyhub repository source code for the TSDZ2 remote and controller. 
> The firmware HEX file to flash is in the github release.

## Bootloader build options
Hex for the combined bootloaded and S340 softdevice flashes are output to the `_build` directory after compilation and linking success.
`NRF_DFU_BL_ALLOW_DOWNGRADE`  will allow the firmware to accept a downgraded version if desired
 `NRF_DFU_BL_ACCEPT_SAME_VERSION`).will allow the firmware to acccept the same version
 `BOARD_USE_SF_CLOCK` is defined to utilize the onboard Soft Device LFCLK.
### TSDZ2 remote control and Controller builds
for both firmwares, the respective MAKE files will automatically put the combined hex file and the signed firmware upgrade zip files in the _upgrade folder after the build process is completed.

## [back](../README.md)

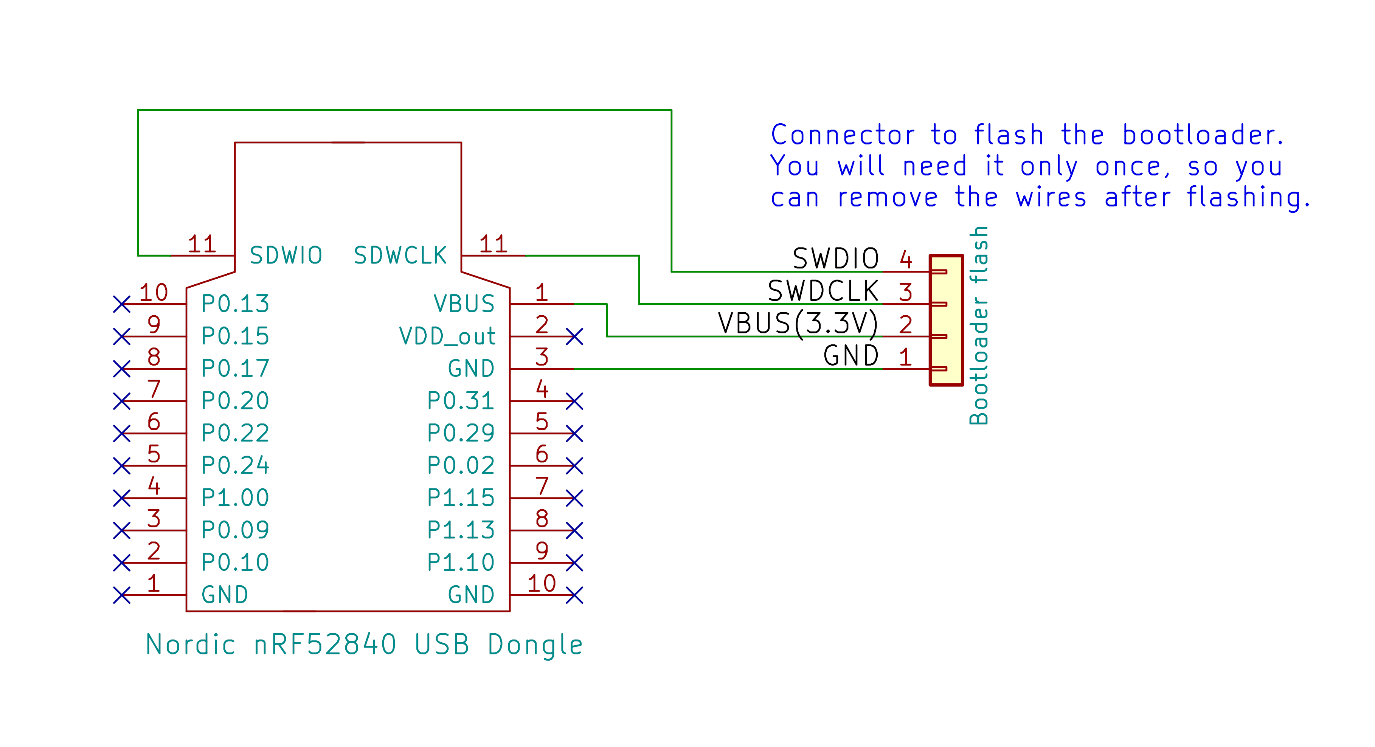
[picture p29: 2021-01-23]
EBike_wireless_bootloader/schematic/Ebike_wireless_bootloader-schematic.png

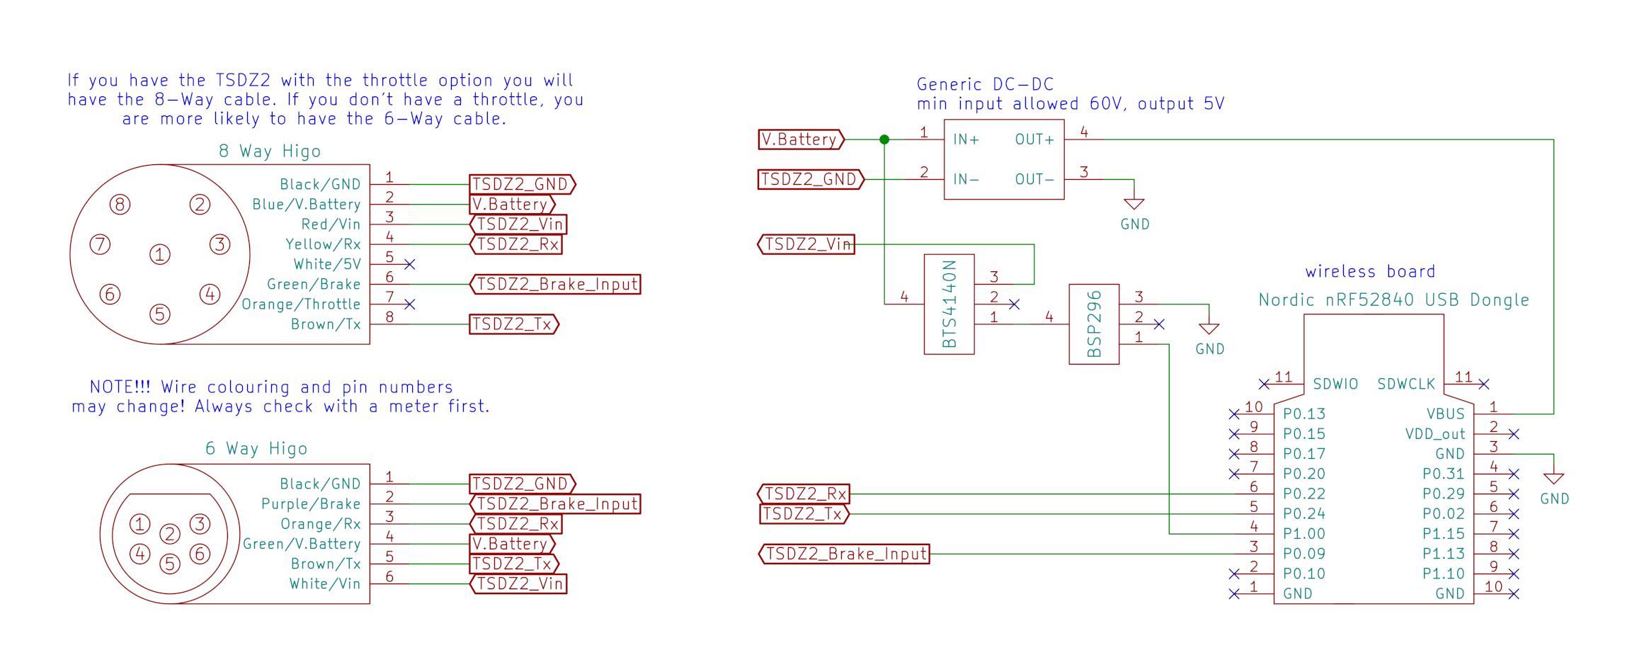
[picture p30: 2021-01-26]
EBike_wireless_TSDZ2/schematic/TSDZ2_wireless-schematic.png

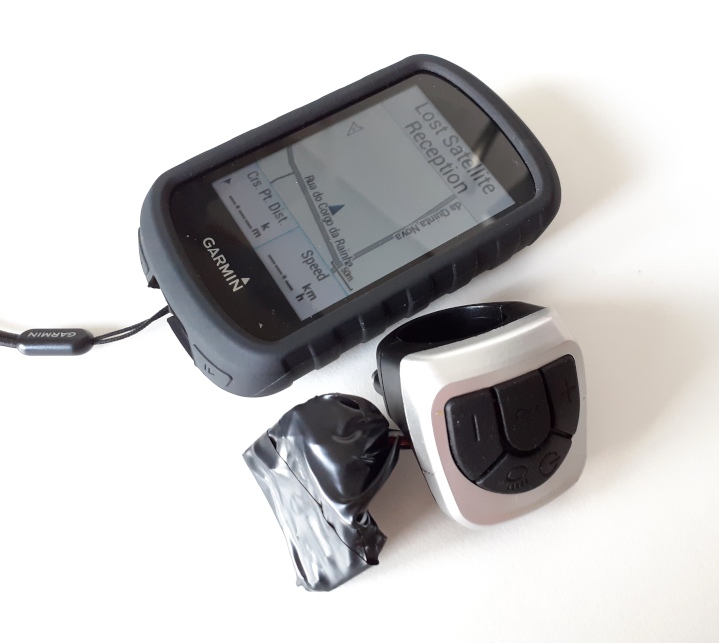
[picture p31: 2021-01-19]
EBike_wireless_remote/hardware/ebike_remote_wireless-picture-v1.png

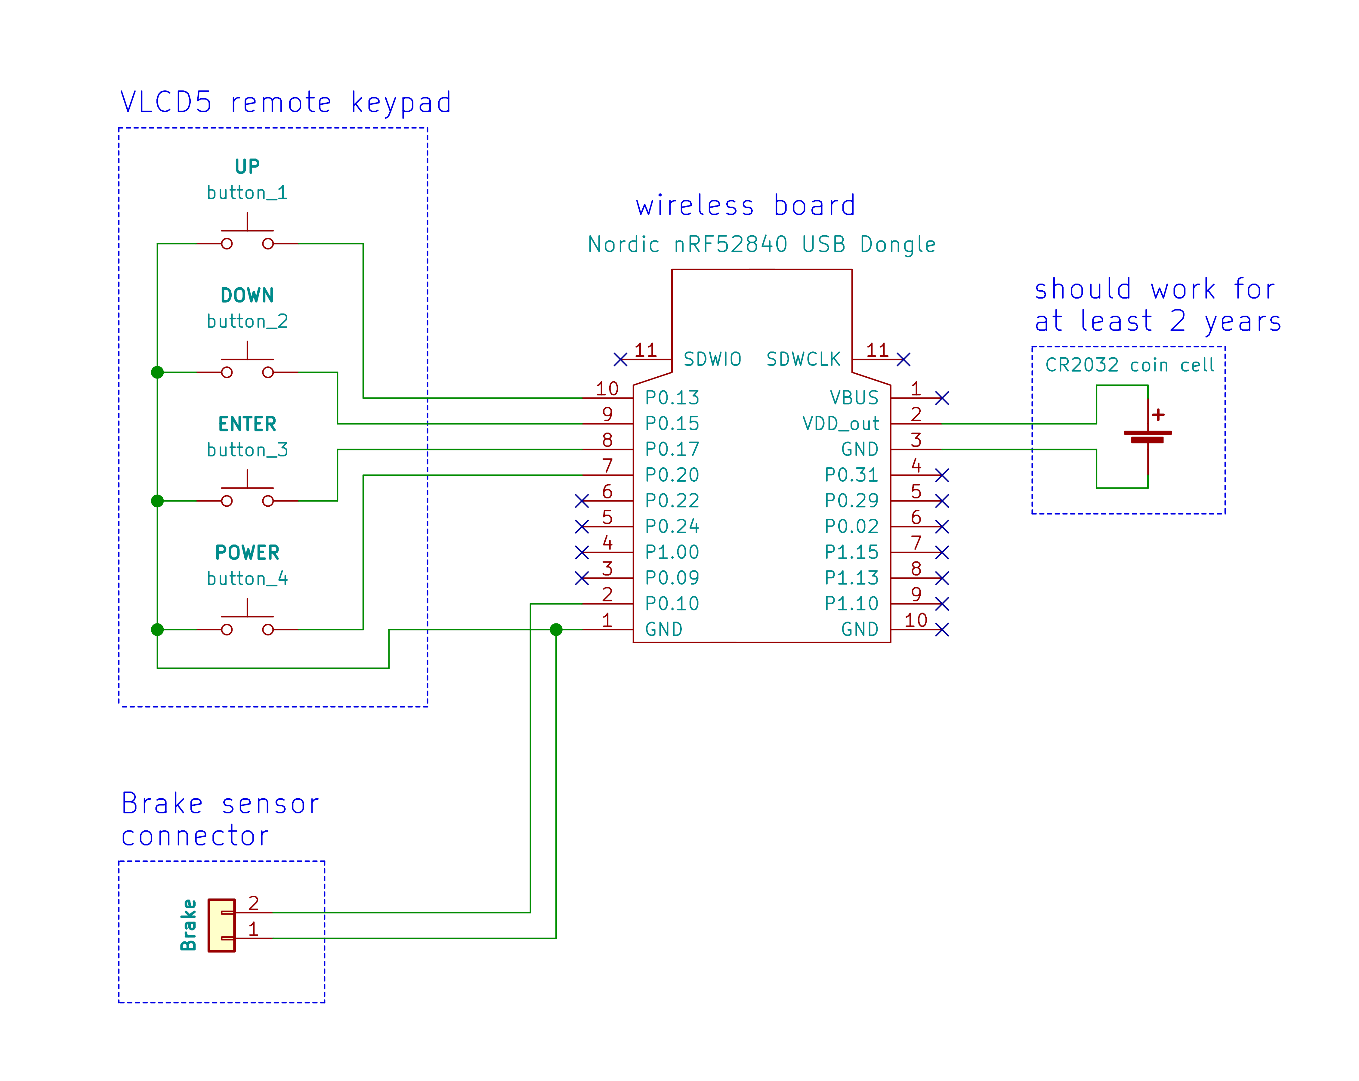
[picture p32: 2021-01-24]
EBike_wireless_remote/hardware/ebike_remote_wireless-schematic.png

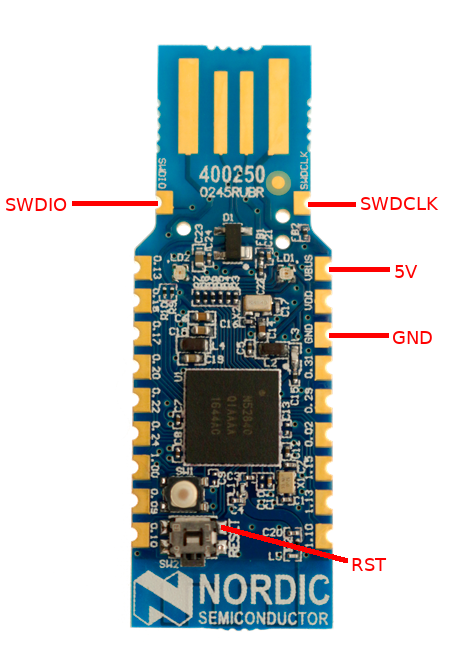
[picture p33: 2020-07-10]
EBike_wireless_remote/documentation/nRF52840 Dongle Pinout.png

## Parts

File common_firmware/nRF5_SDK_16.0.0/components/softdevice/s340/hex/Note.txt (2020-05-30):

D52 Modules using this SoftDevice have been designed to operate in typical 
operating environments up to 30m

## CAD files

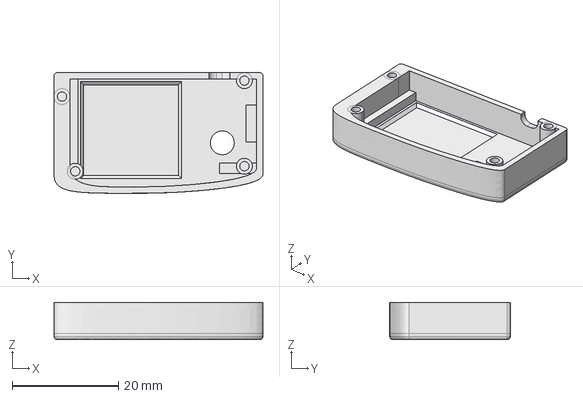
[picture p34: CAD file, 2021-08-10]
EBike_wireless_remote/3d_design/EBike_wireless_remote.FCStd
39.3 x 22.7 x 7.05 mm

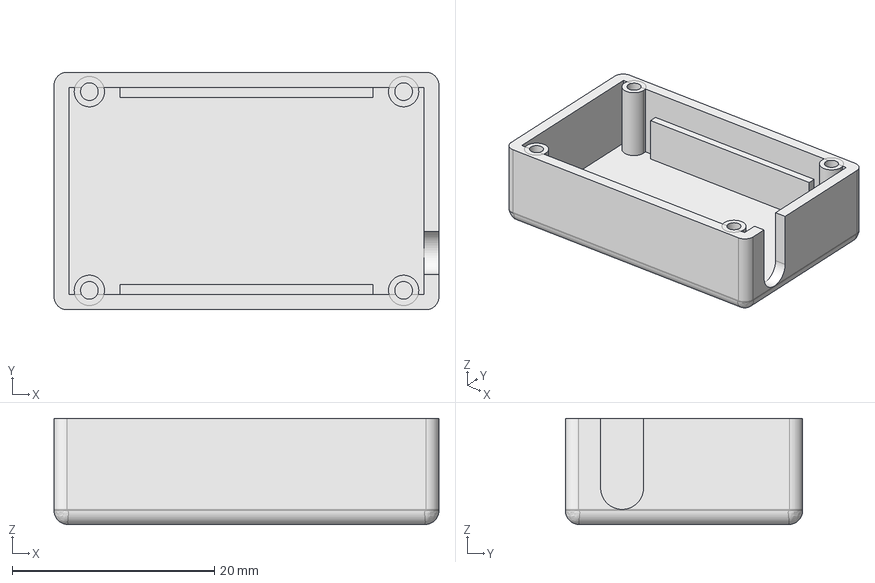
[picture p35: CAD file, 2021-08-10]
EBike_wireless_TSDZ2/3d_design/TSDZ2_wireless_small_box.FCStd
38.1 x 23.5 x 10.5 mm

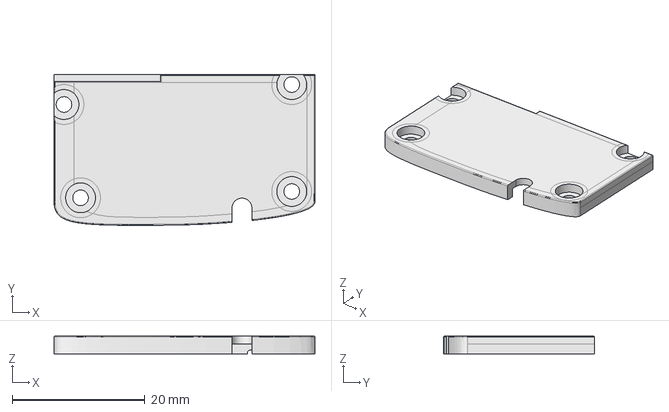
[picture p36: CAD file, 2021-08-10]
EBike_wireless_remote/3d_design/EBike_wireless_remote_cover.FCStd
39.3 x 22.7 x 2.70 mm

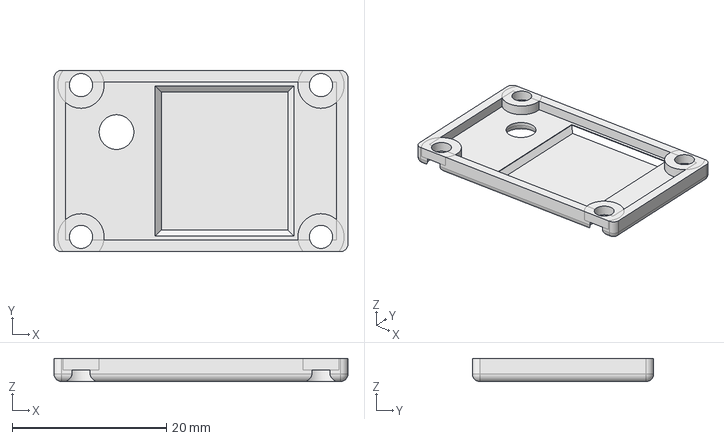
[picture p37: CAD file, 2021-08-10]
EBike_wireless_TSDZ2/3d_design/TSDZ2_wireless_small_box_cover.FCStd
38.1 x 23.5 x 3.00 mm

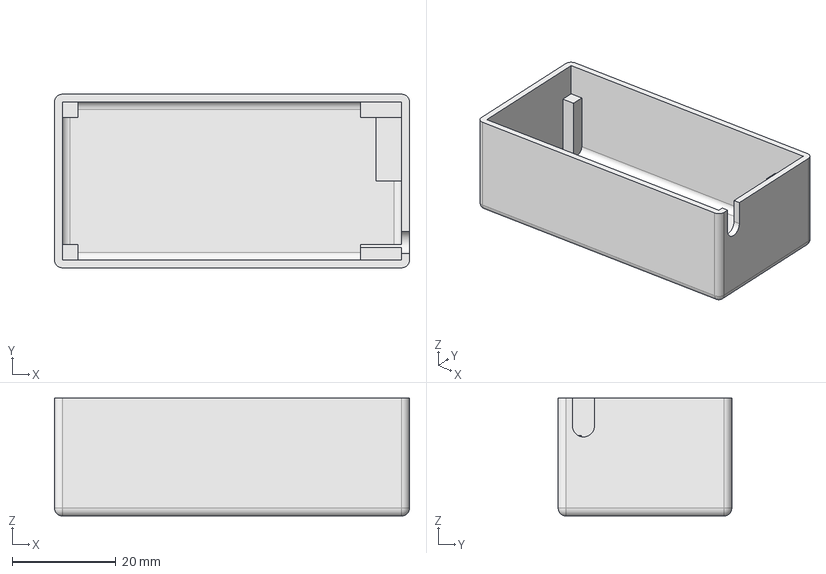
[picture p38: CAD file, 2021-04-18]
EBike_wireless_TSDZ2/3d_design/TSDZ2_wireless_box.FCStd
68.5 x 33.5 x 22.8 mm

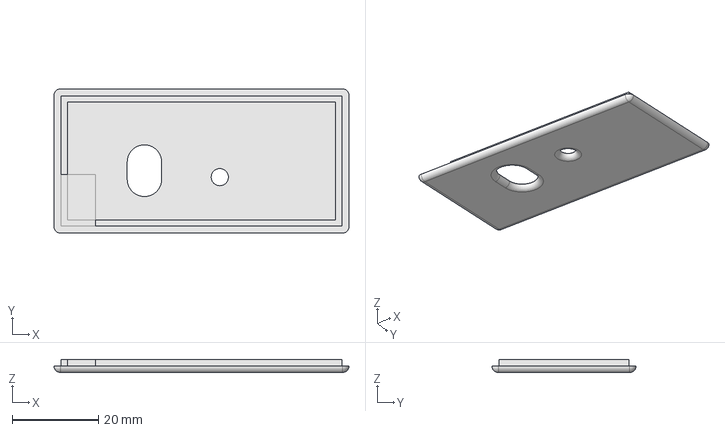
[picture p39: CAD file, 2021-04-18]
EBike_wireless_TSDZ2/3d_design/TSDZ2_wireless_box_cover.FCStd
68.5 x 33.5 x 3.00 mm

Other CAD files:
EBike_wireless_TSDZ2/3d_design/3d_print/TSDZ2_wireless_box.amf
EBike_wireless_TSDZ2/3d_design/3d_print/TSDZ2_wireless_box_cover.amf
EBike_wireless_TSDZ2/3d_design/3d_print/TSDZ2_wireless_small_box.amf
EBike_wireless_TSDZ2/3d_design/3d_print/TSDZ2_wireless_small_box_cover.amf
EBike_wireless_remote/3d_design/3d_print/EBike_wireless_remote.amf
EBike_wireless_remote/3d_design/3d_print/EBike_wireless_remote_cover.amf

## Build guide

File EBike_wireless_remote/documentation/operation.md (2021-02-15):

# **Remote operation**

## Getting started with the Wireless remote 

**To get started , follow this simple four step process (or five steps if you have connected the e-brakes):**
(Please note that buttons will briefly flash **RED** if they are inactive)

1. Ensure that the second wireless board is powered up and connected to the TSDZ2 motor controller. Ensure that the remote has a battery connected and press any button to start the pairing process with the motor controller. When the remote is searching for an ANT connection, the RED LED will slowly flash. When a connection is made with the motor, the GREEN LED will short flash twice followed by one long flash to indicate connection.
2. To turn on the motor from the remote control, press and hold the [POWER]() key on the remote control. A  **YELLOW** LED will start flashing, and will continue flashing until the motor is on, at which time a **GREEN** LED will short flash twice followed by one long flash to indicate that the motor is on.
3. press the [PLUS/MINUS]() keys briefly to increase/decrease the motor assist level. The **GREEN** LED will briefly flash on every [PLUS]() press of the button, while the **YELLOW** LED will briefly flash on every [MINUS]() press of the button. There are 7 levels of assist. When you reach level 7 (maximum assist) or level 0 (motor off) the **RED** LED will briefly flash.
4. (Optional step needed you have connected the e-brakes) Depress either the right or left brake lever. The **RED** LED will flash quickly and the motor assist will stop. Release the brake lever and the **RED** led will turn off and the motor assist will resume.
5. To turn off the motor, press and hold the [POWER]() key on the remote control. The **RED** LED will short flash twice, followed by one long flash to indicate the motor is off. The LED will then flash one flash for every 10% of charge remaining in the battery.(ie:5 flashes=50% charge remaining). The flashes will be **RED** from 0%-40%, **YELLOW** from 40%-70%, and **GREEN** from 70% to 100% of charge.

### **That's basically all you need to get started with the wireless remote.**

Read the "**Button Operation (NORMAL MODE)**" section below for more details on the remote's operation when riding your e-bike.

If you would like to configure the remote, please read the "**Remote Operating Modes**" section next. Please note that the remote will control the motor "out of the box" and no configuration is necessary unless you would like to pair a specific bike computer, set specific ANT configurations, or wirelessly update the remote firmware . Most people can safely ignore **CONFIGURATION MODE** and still enjoy full functionality from their remote.

Have Fun!!

## Remote Operating Modes
The remote has two modes of operation; **CONFIGURATION MODE** and **NORMAL MODE**, for configuration and normal operation, respectively.

----

## NORMAL MODE

----

**General LED button signals:**

* When the motor is off, inactive buttons will briefly flash a **RED** LED when pressed.

* Long Pressing a button will briefly flash a **GREEN** LED to indicate that the button has been pressed
  
----
**Short Press Button Actions:**

* Short Press the [PLUS]() (**GREEN** LED) /[MINUS]() (**YELLOW** LED) buttons to increase/decrease the assist level. If the assist level has reached either 0 or 7, pressing the [PLUS]() or [MINUS]() keys key will cause the led to briefly flash **RED** to indicate the limit has been reached. 
* When the motor is on, hort Press the [POWER]() button to display the motor battery state of charge. Battery state is indicated by flashing. The number of flashes will indicate battery charge state from from 1 flash (10% charge) to 10 flashes (100% charge). The flashes will be **RED** from 0%-40%, **YELLOW** from 40%-70%, and **GREEN** from 70% to 100% of charge.(Motor On **ONLY**.)  
* When the motor is off, double click on the [POWER]() button to put the remote control in 'deep sleep' low power mode. The **RED** and **YELLOW** LEDS will short flash followed by a long flash of the **GREEN** LED to indicated initiation of low power mode.
 * Short Press the [ENTER]() button to **PAGE UP** on a connected garmin bike computer. (Works **ONLY** if garmin control is activated)
 * Double click on the [ENTER]() button to set one of 3 levels for LED intensity. Every  double click will set a new LED intensity. The RED, GREEN, and BLUE LEDs will long flash once so the effect of the new setting can clearly be seen.

**Long Press Button Actions:**

* Long Press the [ENTER]() button to **PAGE DOWN** on a connected garmin bike computer. (Works **ONLY** if garmin control is activated)
* A long press of the [POWER]() key will turn the motor ON or OFF. A  **YELLOW** LED will start flashing, and will continue flashing until the motor is on, at which time a **GREEN** LED will short flash twice followed by one long flash to indicate that the motor is on. If the motor is turning off, The **RED** LED will short flash twice, followed by one long flash to indicate the motor is off. The LED will then flash one flash for every 10% of charge remaining in the battery.(ie:5 flashes=50% charge remaining). The flashes will be **RED** from 0%-40%, **YELLOW** from 40%-70%, and **GREEN** from 70% to 100% of charge.
* Long press the [PLUS]() button to toggle the lights on/off 
* Long press and hold the [MINUS]() button to start the motor walk assist. When walk mode is active the **GREEN**  LED** will flash slowly.Releasing the [MINUS]() button stops walk assist.
* A very long press (more than 5 seconds) of the [ENTER]() button will enter **CONFIGURATION MODE**. The **BLUE** LED will flash rapidly 10 times to indicate thay configuration mode is active.
  
----

## CONFIGURATION MODE

----
In **CONFIGURATION MODE**, the remote has a 2 configuration options, namely specifying a specific ANT ID for use with the ebike and setting up ANT LEV control options. Both of these settings are optional as the remote will default to control the TSDZ2 wireless controller without the need to set anything.

* The ANT ID allows you to pair the remote to a specific TSDZ2 motor. The default ANT ID of 0 allows the remote to pair with any TSDZ2 motor within range. Any other number will cause the remote to ONLY pair with a motor with the same ANT ID. This is a useful option if you have multiple ebikes. The ANT ID can be changed by a bluetooth connection to the remote.
* The ANT LEV control options allow you to pair the remote to an ebike alone, (the default option) , a bike computer (like the Garmin Edge series) , or any combination of these devices.
to enter and exit **CONFIGURATION MODE** press and hold the [ENTER]() button for more than 5 seconds. The **BLUE** LED will flash rapidly 10 times to indicate that configuration mode is active, followed by a visual display of ANT  options. The **RED** LED will flash 5 times to indicate TSDZ2 motor control is active, followed by the **GREEN** LED flashing 5 times to indicate that control of Garmin bike computers is active <br>

----

## Button Operation (CONFIGURATION MODE)

----

* Short press the [ENTER]() key to display configuration options. The **RED** LED will flash 5 times to indicate TSDZ2 motor control is active, followed by the **GREEN** LED flashing 5 times to indicate that control of Garmin bike computers is active
* Long press the [ENTER]() key to leave **CONFIGURATION**  mode. The **BLUE** LED will flash 5 times to indicate you are entering **NORMAL** mode
* Short press the [PLUS/MINUS]() keys to enable/disable garmin control. (The **GREEN** LED will flash 5 times to indicate that garmin control is active)
* Long Press [PLUS/MINUS]() keys simultaneously will enable/disable TSDZ2 motor control(The **RED** LED will flash 5 times to indicate that motor control is active)
* A Long Press of the [POWER]() button will initate Device Firmware Update (DFU) mode.  The **BLUE** LED will flash rapidly 10 times, and the board will enter DFU mode.Either the remote or bootloader firmware can be updated to a new version using a provided upgrade packet zip file in DFU mode. For more information click [here]()(dfu.md).

----

See controlling a Garmin 1030 bike computer for assist levels and page control using a simulated ANT+ LEV Ebike in this video:

[![video]()(https://img.youtube.com/vi/s7URIMVzcwc/hqdefault.jpg)]()(https://www.youtube.com/watch?v=s7URIMVzcwc)

----

See changing the ANT+ LEV Device Number (to connect to only one specific eBike) using the Nordic nRF Connect app in this video:

[![video]()(https://img.youtube.com/vi/_ALauuDxZuQ/hqdefault.jpg)]()(https://youtu.be/_ALauuDxZuQ) 

----

nRFConnect is available on the play store [here]()(https://play.google.com/store/apps/details?id=no.nordicsemi.android.mcp&hl=en_CA&gl=US)

----
## [back](../README.md)

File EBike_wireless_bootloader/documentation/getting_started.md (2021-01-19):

# Installing the Bootloader on the Nordic USB Dongle
**Components you will need:**
* [nRF52840 Nordic USB Dongle](https://www.digikey.com/en/products/detail/nordic-semiconductor-asa/NRF52840-DONGLE/9491124): (costs $10) this is this wireless board
*  [STLINK V2](https://www.ebay.com/c/896036216): (costs $3)
  
  ## Pinout
Board

Pinout

## Flashing the bootloader

* For flashing the firmware, connect the SWDCLK, SWDIO and GND pins to the STLinkV2 and follow the flashing instructions below using either Windows or Linux.
Once the firmware is flashed, the stlink  connection will not longer be required , as all future updates can be done wirelessly over bluetooth. 
````
  The firmware HEX file to flash is "TSDZ2_bootloader_with_sd.hex" 
  located in github releases. 
````
----
[Flashing Instructions for Windows](windows.md)
----
-----
[Flashing Instructions for Ubuntu](ubuntu.md)
----
----
  
## [back](../README.md)

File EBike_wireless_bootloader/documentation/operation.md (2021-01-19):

# Bootloader Operation
 Based on the 'Secure Bootloader' example provided in the Nordic nRF52 development kit. 
- DFU over BLE (bluetooth low energy) OTA 
- DFU using USB (Windows or Unix PC's)
- Bootloader is self upgradable via either OTA or USB Serial
- Bootloader will time out and load a valid application if no DFU is initiated 
- Bootloader will sense pressed button pins on start up.
  If button is pressed then an adjustable timer starts, when timed out enters DFU mode. 
  If button is released before timeout, the bootloader will start the installed application immediately.
- Optionally, the firmware upgrade can be downgradable (`NRF_DFU_BL_ALLOW_DOWNGRADE` Makefile option)

## DFU mode will be initiated by any one of the following:
  ### 1. Bootloader cannot find a valid application to load
  If there is no valid application in flash memory, the bootloader will immediately enter DFU mode.
  ### 2. Bluetooth access in DFU mode
  A BLE packet is used to switch to DFU mode without physical contact. The way it works is pretty simple, to switch, we write to the retention register GPREGRET a flag and then we do a soft reset. Since the retention register keeps its value after the reset, the bootloader will check this value when it booting up after the reset and then can enter DFU mode instead of starting the normal application. This is the same behavior as when we hold the board button and trigger a reset.
  ### 3. Button based DFU 
  If, for any reason, you want to force the firmware into DFU mode, this can be done using the physical button on the board. To enter DFU mode press the button on the board during board reset. A reset can be accomplished by either a power cycle or by pressing the reset button on the board. 

## [back](../README.md)

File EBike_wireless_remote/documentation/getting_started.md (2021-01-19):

# Getting Started
**Components you will need:**
* [nRF52840 Nordic USB Dongle](https://www.digikey.com/en/products/detail/nordic-semiconductor-asa/NRF52840-DONGLE/9491124): (costs $10) this is this wireless board
* 
Board 

*  [STLINK V2](https://www.ebay.com/c/896036216): (costs $3)
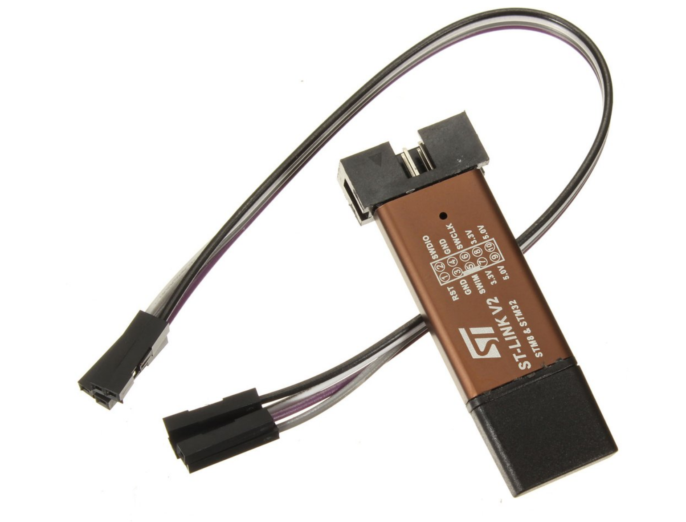
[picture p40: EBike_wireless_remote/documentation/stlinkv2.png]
  
*   [CRC2032 button cell](https://en.wikipedia.org/wiki/Button_cell): (costs $2)
  
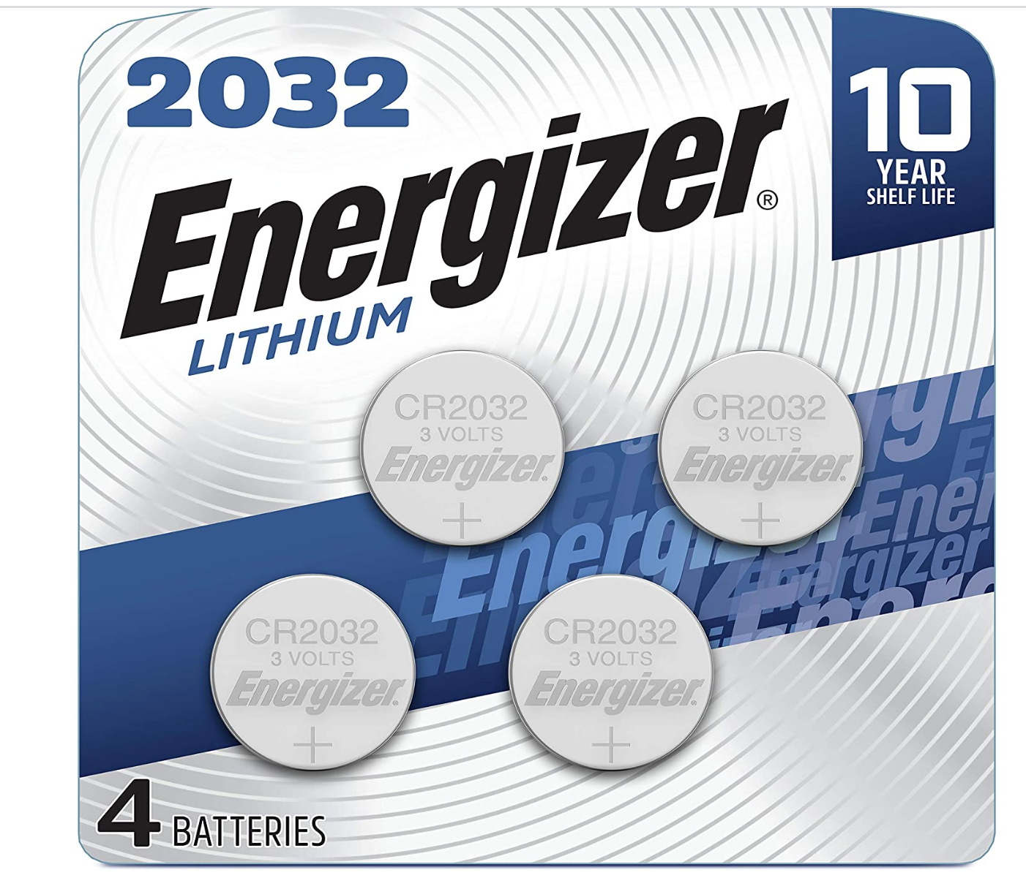
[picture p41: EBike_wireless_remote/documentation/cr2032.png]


* [VLCD5 handle bar remote keypad](https://www.aliexpress.com/wholesale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): (costs $12) can be any keypad that works in the similar way

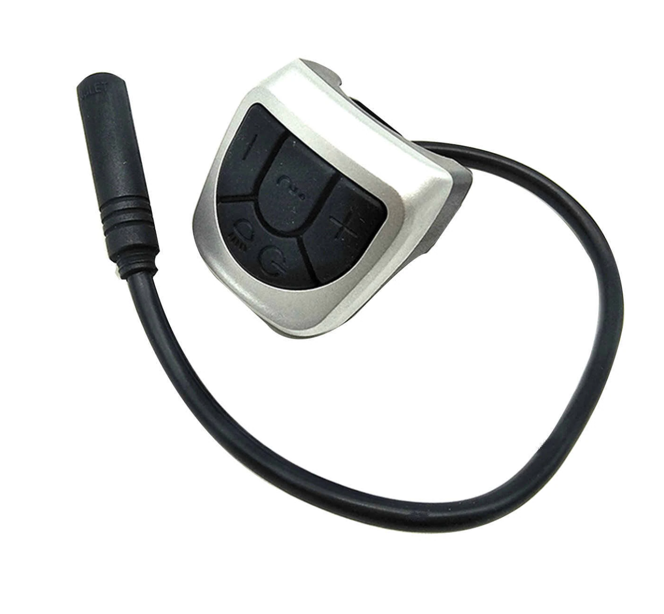
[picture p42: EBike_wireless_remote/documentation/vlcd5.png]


## Board Pinout

Pinout

## Schematic
(need to have a new diagram)

__Instructions:__ 

1. **Install the bootloader on the Nordic nrf52840 dongle**
   To do this, follow the "Installing the Bootloader on the Nordic USB Dongle" link in the bootloader repository located [here](https://github.com/OpenSourceEBike/TSDZ2_wireless-bootloader/blob/main/documentation/getting_started.md)
   
2. **Convert the board to use an external coin battery** 
  You can modify the dongle to use an external 3V CR2032 battery The CRC2032 button cell powers up the wireless board. Connect the cell positive to the VDD OUT pin and the negative to GND.
   
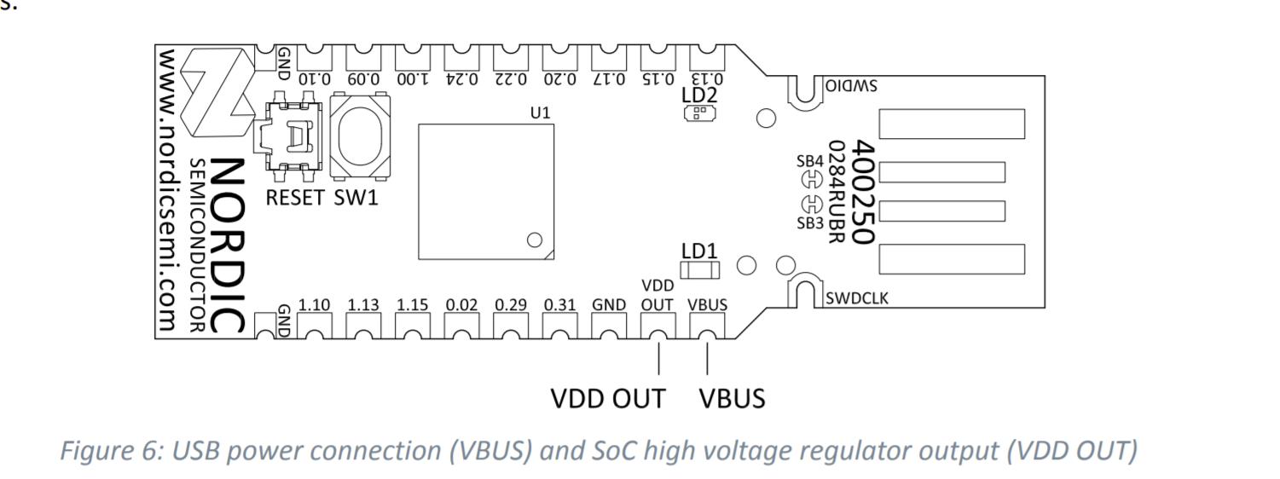
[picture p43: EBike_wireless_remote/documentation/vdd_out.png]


To ensure the dongle has the longest possible battery life it is necessary to cut the SB2 pad on the bottom of the board to open the circuit.

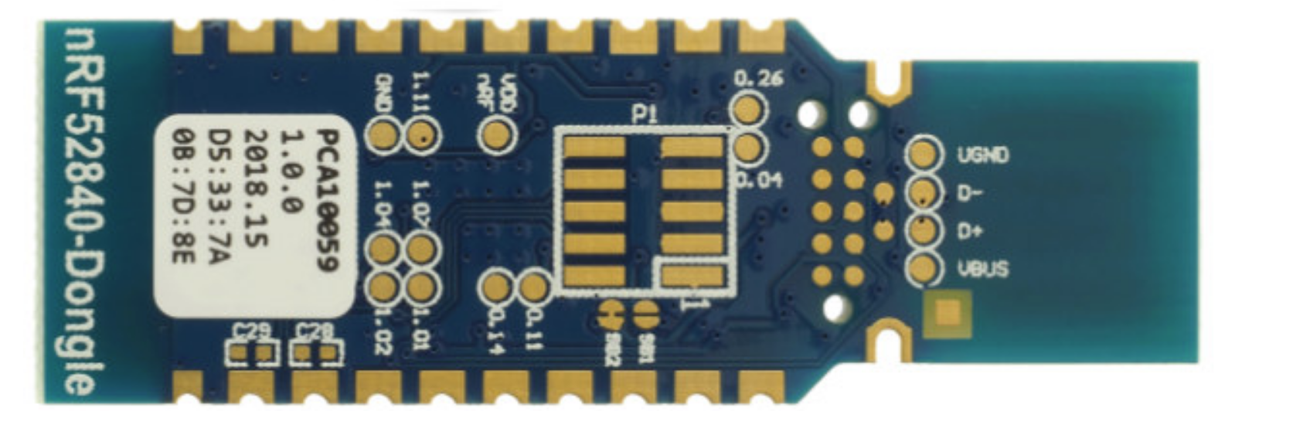
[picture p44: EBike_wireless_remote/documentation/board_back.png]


__Why do we need to cut SB2?__
Please note that the usual power supply of the nRF52840 Dongle is 5V supplied to the VBUS pin of the dongle; see the [schematic for the dongle](./pca10059_schematic_and_pcb.pdf). VBUS supplies power to a on-chip high voltage regulator of the nRF52840 SoC. The output of this regulator (3.3V) supplies the SoC and the LEDs. The cut on SB2 opens the connection to the high voltage regulator and greatly improves power dissipation when using an external battery (Power off mode dissipation improves from ~10uA to ~0.5uA - a 10X improvement. This improves the battery life from 1 to over 2 years!)
 
3. **Connect the VLCD5 keypad**
   The VLCD5 handle bar remote keypad has 4 buttons and 5 wires (1 wire for each button and 1 common wire to all buttons). Connect the wires directly to the Nordic nrf52840 dongle. The pins to connect are 0.13, 0.15, 0.17, 0.20 and GND, corresponding to **PLUS, MINUS, ENTER and STANDBY** buttons on the remote keypad
4. To flash the initial remote firmware, solder the **SWDIO, SWDCLK and GND** wires to the STLinkV2.  (Once the initial remote firmware is flashed, all future firmware updates can be done wirelessly.) Flash the firmware using the bluetooth "Device Firmware Upgrade" (DFU) process.
The bluetooth "Over The Air" (OTA) firmware zip file to flash is **TSDZ2_wireless_remote_ota_update.zip** located in github releases. 
Follow [this procedure](dfu.md) to load the wireless remote firmware on the Nordic nrf52840 dongle.
  
## [back](../README.md)

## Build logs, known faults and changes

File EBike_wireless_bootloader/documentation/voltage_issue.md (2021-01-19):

# Flash Erasure Considerations

#### Overview
 Using the OPENOCD command "mass erase" to clear flash memory will clear the UICR region and reset the voltage regulator from 3.3V to 1.8V output.  This is too low to be used with the external programmers like the ST-LINK, so erasing or programming with a firmware that does not configure the regulator for a higher VDD will leave it in a state where it cannot be re-programmed. The good news is the lower voltage only takes effect AFTER the board is reset. Therefore, to avoid this problem,be sure to flash the bootloader beeore resetting the dongle

#### Detailed explanation
 When you mass erase the chip, it clears the User Information Configuration Registers (UICR).  This includes the RegOut0 register which controls the chip’s voltage regulator output.  This was set to 3.3 V at the factory, but when it’s cleared, the default value is 1.8 V which is too low to be compatible with the ST_LINK.  Fortunately the settings don’t take effect until the chip is reset and when the TSDZ2 bootloader is flashed it will set the regulator back to 3.3 V. This is done using the BSP_BOARD_INIT function, specifically the gpio_output_voltage_setup in boards.c.
  However, if the dongle is reset , unplugged or something goes wrong before flashing the bootloader then the chip will basically be bricked and there would only be 2 recovery options. 

1. You can modify the dongle to use an external 3.3 V power supply through the VDDOUT pin.  This is accomplished by cutting the SB2 trace on the bottom of the board and soldering together SB1.
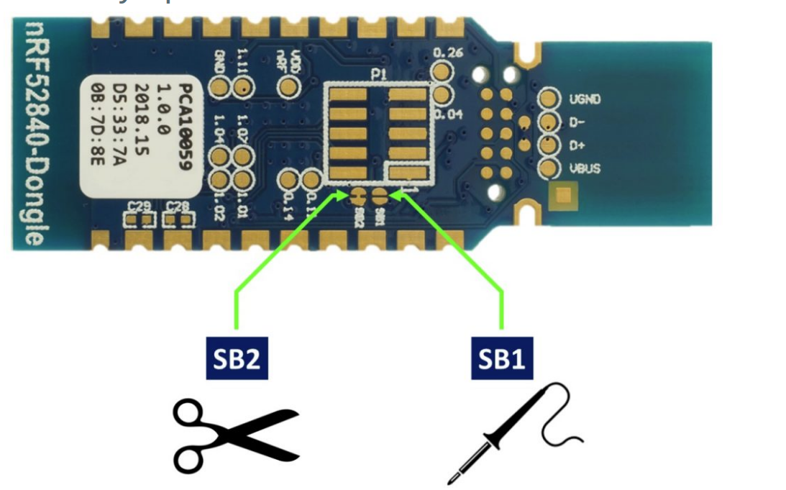
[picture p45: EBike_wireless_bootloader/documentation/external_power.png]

The default power supply of the nRF52840 Dongle is the 5V USB power supply (VBUS); see the [schematic for the dongle](./pca10059_schematic_and_pcb.pdf). VBUS supplies power to the on-chip high voltage regulator of the nRF52840 SoC. The output of the regulator supplies the SoC and the LEDs. VBUS is also available along the board edge.
 
 Next to VBUS, there is a connection point for VDD OUT, which is either the output of the nRF52840 SoC high voltage regulator, or the voltage INPUT for an external source like a cr2032 battery, depending on the state of the SB1 and SB2 bridges. 

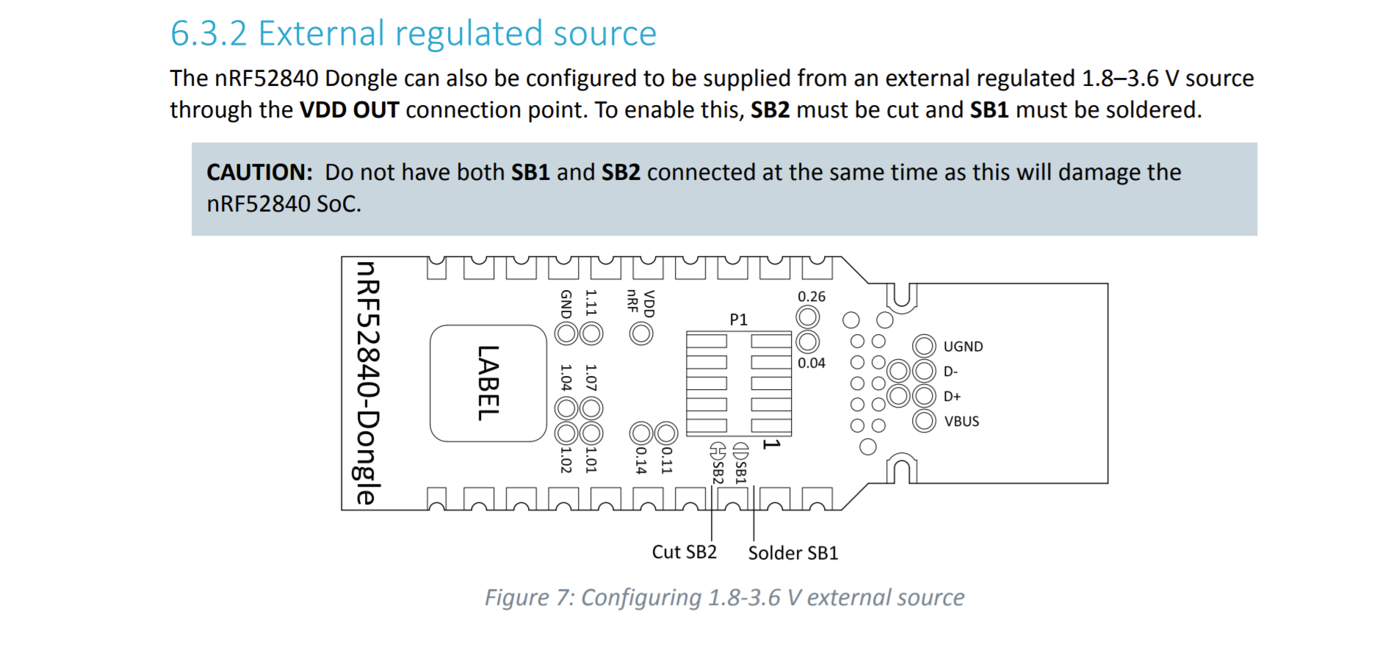
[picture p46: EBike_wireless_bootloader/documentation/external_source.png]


2. Alternatively, you could use a debugger that supports level shifting such as the J-link EDU which has a target voltage range of 1.2 to 5 V. The J-link Mini won’t work because its minimum target voltage is 3.3 V. Another option is to use a level shifter board between the ST-LINK and the nRF52840 dongle.

## [back](../README.md)

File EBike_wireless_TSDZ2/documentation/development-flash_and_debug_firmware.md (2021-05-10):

# Configure Code Studio IDE for firmware development, flash and debug

For the firmware development, flash and debug, you can use the OpenSource and free IDE [Visual Studio Code](https://code.visualstudio.com/). For sure that others will work like the Eclipse.

This guide assumes you are using Linux Ubuntu (if you are on Windows or such, the install process should be similar).

Please see [here](./development_Windows10.md) for a Windows 10 toolchain.

## Software to install

- Add your user to the dialout group: __sudo usermod -a -G dialout USER_NAME__ and reboot
- install [Visual Studio Code](https://code.visualstudio.com/)
  - install C/C++ extension (to edit C/C++ source files)
  - install Cortex-Debug extension (to be able to debug ARM microcontroller)
  - install Task Manager extension (to call makefile and other commands)
- install OpenOCD (to connect to STLinkV2): __sudo apt-get install openocd__
- install GDB GNU debugger (for debug and connect to OpenOCD): __sudo apt-get install gdb-multiarch__
- install ARM C/C++ GCC compiler: __sudo apt-get install gcc-arm-none-eabi__
- install ARM binutils: __sudo apt-get install binutils-arm-none-eabi__
- install ARM newlib: __sudo apt-get install libnewlib-arm-none-eabi__
- install srec_cat tool: __sudo apt-get install srecord__

## Open project folder with Visual Studio Code

Click on menu File -> Open folder... and select the firmware directory. You should see the firmware similar to this:

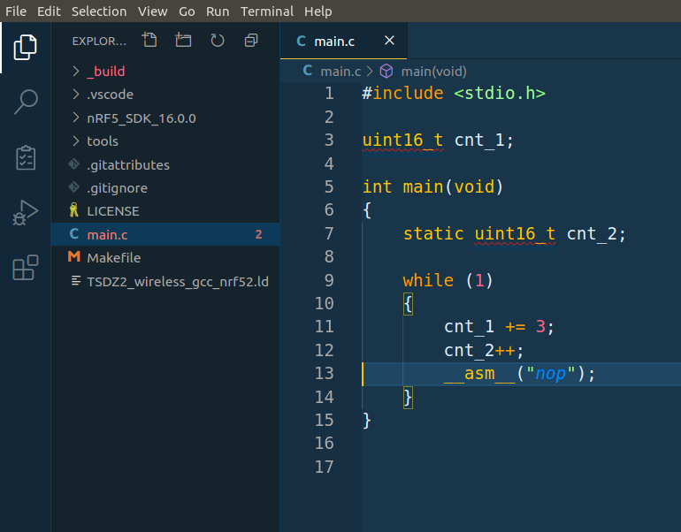
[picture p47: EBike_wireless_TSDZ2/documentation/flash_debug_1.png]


## Build the code

Because you installed the Task Manager extension, you should see Task manager icon on the left bar - click on it. The build, clean and Launch OpenOCD tasks should be available.

Start by clicking on the clean to clean the code and then click on the build to build the code and you should see something similar to this - note the output on the terminal:

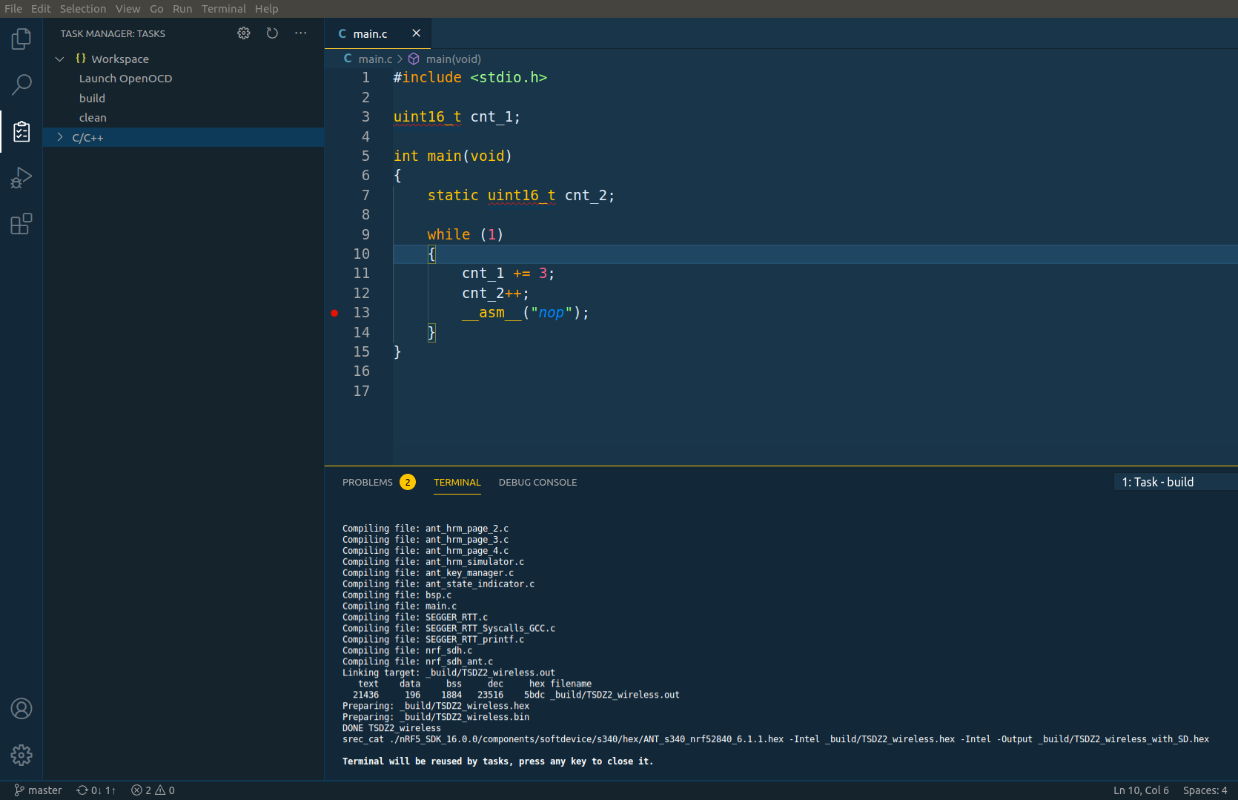
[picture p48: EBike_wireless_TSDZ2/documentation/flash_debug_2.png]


The clean and build tasks call the __make clean__ and __make__ on the terminal. The tasks configurations are on the file .vscode/tasks.json.

## Flash the firmware and debug

1. Connect the STLinkV2 to the board. If you have a nRF52840 MDK Dongle see the pinout in the schematic folder. If you have the blue nRF52840 Dongle it has a different pinout, see [nRF52840 Dongle Pinout.png](./nRF52840%20Dongle%20Pinout.png), note that you do not need to connect the RST pin.

Note that you will also need to install the STLinkV2 udev rules file that are on the firmware/tools/ folder, so the STLinkV2 can be accessed by the OpenOCD:
```
sudo cp 60-st_link_v2.rules /etc/udev/rules.d
sudo udevadm control --reload-rules
```

2. Click on the task Launch OpenOCD

You will need to click only once. The OpenOCD should connect to the microcontroller and keep active - see the example output of OpenOCD on the terminal, when a correct connection was done with the microcontroller:

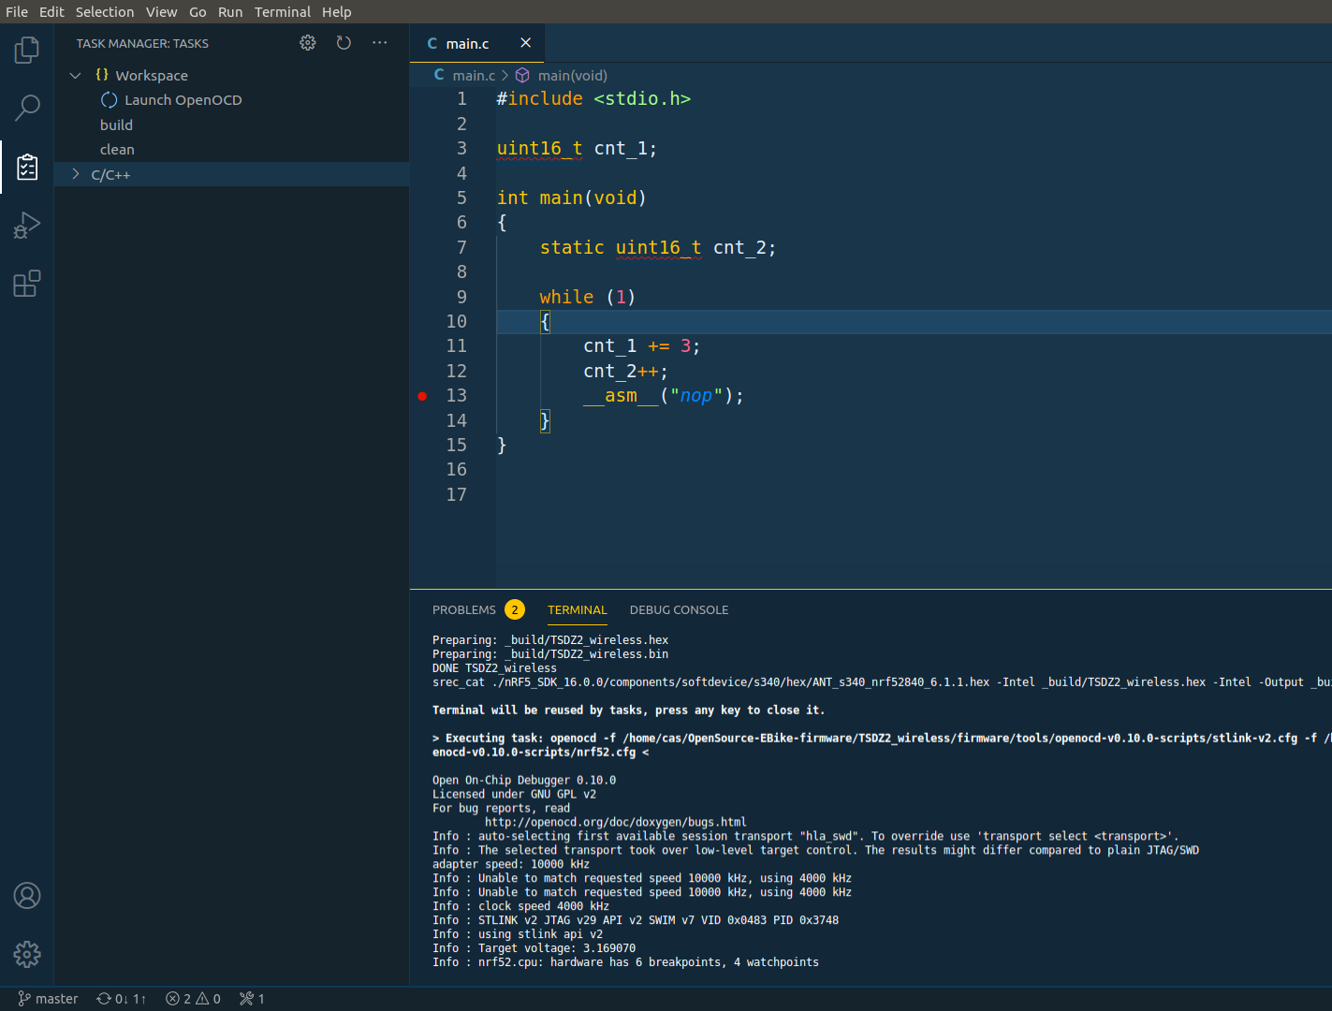
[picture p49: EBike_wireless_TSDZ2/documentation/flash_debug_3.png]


The task Launch OpenOCD configuration is on the file .vscode/tasks.json.

3. Click NRF52 Flash and Debug

Click on the debug icon on the left panel and then click on the small green arrow for the NRF52 Flash and Debug - will flash the firmware on the microcontroller and then start the debug of the firmware.. Wait a few seconds and you should see something like this:

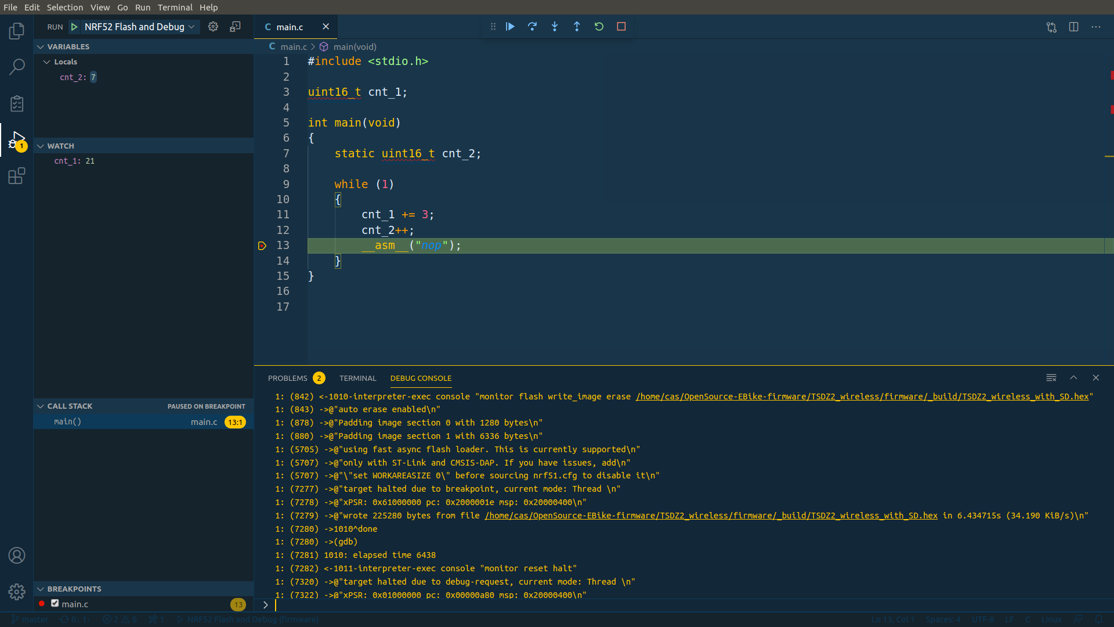
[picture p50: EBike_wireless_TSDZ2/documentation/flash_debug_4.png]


The NRF52 Flash and Debug configuration is on the file .vscode/launch.json.

## Troubleshooting

### Flashing appears to work fine but I cannot debug
If you are flashing code via your STLinkV2 but unable to debug as when you pause the debugger it stops in unknown code you cannot step through (you see the error `ERROR: Unexpected GDB output from command "-exec-next". Cannot find bounds of current function`) then the issue is that your bootloader is doing CRC validation which fails and then refusing to load your code. You have two options to fix this:

1. Change the makefile to generate the bootloader settings with correct CRC in e.g. (you will need to install nrfutil `pip install nrfutil`)
```make
TSDZ2_with_SD:
  nrfutil settings generate --family NRF52840 --bootloader-version 0 --bl-settings-version 1 --application $(OUTPUT_DIRECTORY)/TSDZ2_wireless.hex --application-version 4294967295 $(OUTPUT_DIRECTORY)/settings.hex
  $(SREC_PATH)srec_cat $(OUTPUT_DIRECTORY)/settings.hex -Intel $(SOFT_DEVICE) -Intel $(OUTPUT_DIRECTORY)/TSDZ2_wireless.hex -Intel -Output $(OUTPUT_DIRECTORY)/TSDZ2_wireless_with_SD.hex
```
2. Or flash a more permission bootloader which doesn't do CRC checks using the dfu/open_bootloader/pca100059_usb_debug example from the SDK.

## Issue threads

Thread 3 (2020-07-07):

Schematic: bts4140

jsb1, 2020-07-07:
Hey, cool what You are doing there!

Just a little hint:
The bts4140 cannot be controlled directly from MCU. You must put a small high-voltage Mostfet (BSS100?) in between and reverse the Logic.
How much current has to be switched by the bts4140? Maybe a simple pnp and two Resistors would be a simple replacement.

With best Regards,
 Jörg

casainho, 2020-07-12:
Thanks. Yes, I just found that when I tested. I used a small MOSFET like BSS100 and it worked. The schematic will be updated.

Closed 2020-07-12.

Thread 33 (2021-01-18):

Add New ANT LEV page

rananna, 2021-01-18:
Add a new ANT LEV page to communicate motor state information to the remote control.
Test to confirm that the new page does not interfere with normal ANT LEV communication with other devices

rananna, 2021-02-23:
I investigated implementing this, and although it is possible, leaving the customised control bits (walk mode/motor on/off control, brake control) as it is using  a page 16 acknowledged command is the better option.
Currently I am using the "display command" byte that allows ant lev displays to send commands directly  to an ANT LEV motor, and receive an acknowledgement back. tHIS IS VERY USEFUL, ESPECIALLY FOR THE BRAKE!

There are several options available for the display command byte:
5.10.3 Display Command
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

Two possibilities exist for customized control bits:
1. bits 10-15 that are 'reserved' for future use
2. the gearing control bits that are intending to allow a user to change the front or rear gearing by ant lev control
since the TSDZ2 ant lev motor does not have a gearing option this creates no conflict with future use.
also, commercial gear shifters like the shimano di2 using a proprietary ant+ profile, so there is no conflict with ant lev.
the sram etap uses the garmin ANT+ SHIFT profile, so again no conflict.
The only potential future issue is if we add a ANT_LEV motor with electronic shifting, not very likely at all.

so, although we could also modify the code to use bits 10-15, or add another ANT+ LEV page to the standard,  there is little downside for now in keeping things as they are and continue to use the gearing bits.

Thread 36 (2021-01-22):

add temp sensing

rananna, 2021-01-22:
The ANT LEV standard suppords motor temperatures.
Add this capability,  perhaps using the existing throttle hack that would make it downward compatible with existing motors.

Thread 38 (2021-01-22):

add travel range

rananna, 2021-01-22:
Add ANT LEV travel range field.
This could be used as stated for travel range, or perhaps use it to display human power as this may be of more interest.

casainho, 2021-01-22:
I would follow the standard and put there only the expected data.

Maybe we can implement fields for Garmin, that connect by Bluetooth to the wireless board and receive like motor power, battery SOC, motor temperature in ºC.

rananna, 2021-02-06:
Done.

Closed 2021-02-06.

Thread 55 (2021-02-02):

Connect IQ page

rananna, 2021-02-02:
Implement Bluetooth CONNECTIQ data field for edge bike computers to transfer current, human power, motor power, voltage etc. This would allow for display of all the missing info

casainho, 2021-02-02:
Yes!! This is a must!!

The question is: will be ANT or Bluetooth? I don´t think ANT+ will work because we will be doing very specific things.

rananna, 2021-02-02:
Unfortunately, I don't think this can be ANT+ as custom fields are not possible with the edge bike computers. You are restricted to using existing ANT + sensor profiles.
However, you could design a customized blue tooth connect iq profile like the one that @jancapek designed.
Perhaps we should try to reach out to him as he expressed interest in helping.
( search for his dec 01 post on the forum)

rananna, 2021-02-02:
I just sent him a message asking him to reach out on the forum if he is interested in helping out.

casainho, 2021-02-02:
Here the source code for a simple Garmin data field that writes to a Bluetooth characteristic: https://github.com/fabiobaltieri/ciq-nrf-blinky

See how simple it is: bleDevice.setLed(1); and bleDevice.setLed(0);

We need the inverse, to read a characteristic but this source code seems a very good starting point!!

rananna, 2021-02-05:
implemented an ANT+ ConnectIQ data field

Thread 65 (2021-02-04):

Remote unresponsive

casainho, 2021-02-04:
I do not know how to replicate but did happen 3 times to me. I think is when I decrement a few times in sequence and then there is no response (no blink from any button).

casainho, 2021-02-05:
I tested again, seems an issue easy to replicate: change assist level when motor is turned off.

rananna, 2021-02-05:
sorry, I do not understand. Per your request, the remote currently does NOT change assist level when the motor is off.
It simply flashes red.

rananna, 2021-02-05:
I will try to see if I can do something more about interrupt priority for  GPIO so that button presses are not missed.
As discussed previously, this is a known Nordic issue when using a softdevice.
The softdevice has the highest priority, and if it is still processing communication events it locks out the button interrupt.
Any button press that is captured is setting the assist level though, there is no missing assists no matter how may up/down combinations are made.

rananna, 2021-02-05:
When I press the button quickly with the motor off, I do not see any missing red flashes.
Is that what you are referring to?

rananna, 2021-02-05:
And, are you using the latest firmware for the remote?
I made the interrupt priority and assist capture changes only recently.
I am not seeing any issue with the motor on also

rananna, 2021-02-05:
button high accuracy mode can improve responsiveness, but has a BIG power impact.
I don't think we want this.

rananna, 2021-02-07:
OK, I think this has been addressed.
Please check with my FEB 7 PR

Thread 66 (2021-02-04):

Remote stop assist level

casainho, 2021-02-04:
Did happen a few times to me, suddenly there is not assistance from the motor. On Edge I always see an assist level like 3. I increase the assist level and then I get the assist from motor and on Edge I see assist level 4. I always get assistance after increasing the assist value.

rananna, 2021-02-05:
is this related to the 0.028 bug in assist 3 (for the android app) that was identified?
There is absolutely no difference in how the assist level is generated for any of the levels for the remote

4var1, 2021-02-07:
Did you have the wired button code running in the wireless controller? Might well be fixed by the PR I just submitted - could well affect even if you don't have any buttons connected to the wireless controller...

rananna, 2021-02-16:
can't reproduce this issue.
Have you seen it with the latest code?

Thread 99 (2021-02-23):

leds will not light

rananna, 2021-02-23:
@4var1 , If you call led_sequence_next two times in a row, the led sequence will no longer function.

4var1, 2021-02-24:
I call play next repeatedly with no issues - I can mash the buttons and it keeps playing the assist sequences... things get queued up as expected.

  if (handled == false)
  {
    if (events & UP_CLICK) {
      ui_vars.ui8_assist_level++;

      if (ui_vars.ui8_assist_level > ui_vars.ui8_number_of_assist_levels) {
        ui_vars.ui8_assist_level = ui_vars.ui8_number_of_assist_levels;
        led_sequence_play_next(LED_EVENT_ASSIST_LIMITS_REACHED);
      }
      else led_sequence_play_next(LED_EVENT_ASSIST_LEVEL_INCREASE);

      handled = true;
    }

    if (events & DOWN_CLICK && !ui_vars.ui8_walk_assist) // do not lower assist level if walk assist is active
    {
      if (ui_vars.ui8_assist_level > 0)
      {
        ui_vars.ui8_assist_level--;
        led_sequence_play_next(LED_EVENT_ASSIST_LEVEL_DECREASE);
      }
      else led_sequence_play_next(LED_EVENT_ASSIST_LIMITS_REACHED);

      handled = true;
    }
  }

4var1, 2021-02-24:
doing a few tests just to double check

4var1, 2021-02-24:
> doing a few tests just to double check

@rananna - ok does seem that if you call them in succession something odd happens - I'll repot back later this morning with findings!

4var1, 2021-02-24:
ok - i can see why it happens - it's because we changed the sequencer to sit on an interrupt. So there isn't a synchronous call to start playing - we queue and in the background wait for the sequencer to fire and start it playing.

So when we call two next in quick succession - the first doesn't get a chance to play because there isn't time for the sequence ISR to fire and register the sequence playing - so it gets lost.

4var1, 2021-02-24:
@rananna - ok am off in training again all day so won't be online - but i've submitted a PR that 'fixes' the issue. It's not a nice fix - but does solve the current problem. I'll work on a better fix later this evening.

https://github.com/OpenSourceEBike/TSDZ2_wireless/pull/101/files

Closed 2021-02-27.

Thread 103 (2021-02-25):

walk assist is intermittently working

rananna, 2021-02-25:
@4var1 , @casainho ,This is a strange one.
Wlak assist will work fine once, and then stop working.
This happens with both the wired and wireless remotes.
@4var1 , could you please try this to see if it happens to you?

4var1, 2021-02-25:
OK do you mean the assist stops working, or the flashing leds or both? I
just did a quick test on my spare motor (doesn't have 48v supply so motor
doesn't spin) and walk assist flashing leds worked fine, tested 3 or 4
times in succession.

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

rananna, 2021-02-25:
Boy, I need to be more precise in my description!
What I mean is that the motor works fine ONCE, then stops working.
I wondered if it had something to do with the mysterious delay variable set to 2.
Anyway, maybe it's my setup, so I wondered if either of you were seeing any issues with the motor in walk mode.
LED signalling works fine for this mode.

4var1, 2021-02-25:
OK I'll try to find some time tomorrow to flash the bike and see what's
what. I guess I should give ota flashing a go too... I'm still using swd
all the time

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

4var1, 2021-02-25:
I connected a 48v supply to my test motor, walk assist works fine
repeatedly, motor and leds activating OK.

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

rananna, 2021-02-25:
Ok must be something associated with my build. Thanks for looking.

4var1, 2021-02-25:
Just merged the latest changes and still works OK. As for timeout for me
there is only a delay before walk assist starts working. Any break in
button press results in stop of walk assist. Doesn't seem to be any 2s
period where button release is ignored.

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

rananna, 2021-03-02:
I am still seeing walk assist working intermittently.
It will work fine 2 or 3 times in a row, then stop working.
rebooting the motor firmware will get it working again.
Can't imagine what is going wrong on my end.
Will keep this issue open for now....

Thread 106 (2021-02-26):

Very strange bug!

rananna, 2021-02-26:
@casainho , On the forum you asked me to change TSDZ2_FIRMWARE_MAJOR := 0
TSDZ2_FIRMWARE_MINOR := 6 in the makefile for the wireless controller
Previously, I had these set to 1 for both.
When I do this, the motor will not go out of initializing when I try to turn it on
When I set them to 1 everything is fine.
It is only a CFLAG, what is going on??

rananna, 2021-02-26:
Could this be the source of the strange issues we are seeing on the forum?

casainho, 2021-02-26:
I need to check when I am at the computer... Maybe just tomorrow.

rananna, 2021-02-26:
On the forum I just confirmed a successful flash of the wireless remote.
The wireless controller still has issues, maybe it is somehow related to this?

casainho, 2021-02-26:
APP_VER_MAJOR / MINOR and not TSDZ2_FIRMWARE_MAJOR / MINOR!!

Maybe the bootloader has some bug and needs increase of APP_VER_MAJOR / MINOR, that was some idea I had.

bl_settings:
	$(SREC_PATH)nrfutil settings generate --family NRF52840 --application $(OUTPUT_DIRECTORY)/TSDZ2_wireless.hex --application-version-string $(APP_VER_MAJOR).$(APP_VER_MINOR).0 --bootloader-version 1 --bl-settings-version 2 $(OUTPUT_DIRECTORY)/bl_settings.hex

OTA:
	$(SREC_PATH)nrfutil pkg generate --hw-version 52 --sd-req 0xB9 --application-version-string $(APP_VER_MAJOR).$(APP_VER_MINOR).0 --application $(OUTPUT_DIRECTORY)/TSDZ2_wireless.hex --key-file private.key --app-boot-validation VALIDATE_ECDSA_P256_SHA256 $(OUTPUT_DIRECTORY)/TSDZ2_wireless_ota_update.zip

rananna, 2021-02-26:
What does tsdz2_firmware_major/minor do?

rananna, 2021-02-26:
I will give him an updated file to try.

casainho, 2021-02-27:
tsdz2_firmware_major/minor - at boot, display asks motor controller for his firmware version and checks against this, only initializes the motor / sends the configurations, if the version is correct, otherwise gives an error.

rananna, 2021-02-27:
Checked bootloader code.app. version shouldn't cause any issue. Had user try  higher/lower version. Still an issue.
He can flash wireless remote firmware, but not the controller.
Ran out of ideas.

casainho, 2021-02-27:
I think you should focus on the next release for today and tomorrow - I can test it tomorrow. Then we will see as everyone of us will be using it.

rananna, 2021-02-27:
Ok.
No more changes expected from me.
 I will test again today that I be sure everything works.

On the other topic found this on the Nordic site:
https://devzone.nordicsemi.com/f/nordic-q-a/58618/dfu-upgraded-app-wont-boot

We use -o0, maybe try -o3?

Of course, an important question to answer is  why are we not having the same issue?

Closed 2021-02-26.

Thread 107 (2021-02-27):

For general Communication

rananna, 2021-02-27:
@4var1 ,  @casainho , There is no way to PM users on github. We have been using PR comments for this and this results in difficulty finding messages. On the github forum they recommend creating an issue to track communications, so here it is!

Anyway, my first message is that I have just completed tesiting the wireless remote for use as a release.
@casainho , It all test well and is ready for your ride tomorrow.

rananna, 2021-02-27:
@casainho , @4var1 ,

For reference, here is what has been tried (and didn't work) for flashing the wireless controller with Filippods on the forum:
1. downgrade rev lev
2. upgrade rev level
3. optimized firmware ( -o3 set)
4. released 0.6.2 firmware
5. latest firmware (release candidate)
6. latest wireless remote firmware (this DID work, suggesting he is flashing with nrf connect ok, and that something is different with the controller OTA update firmware, but I don't know what that would be....)
7. different 5v supply
8. a second board (he may have damaged two boards, but the bootloader TSDZ2_DFU appears in both cases strongly suggesting the boards are fine)

no errors seem to occur in nrf connect, however he does not see TSDZ2 in bluetooth after flashing.
No leds light up in the latest firrmware

I tried reproducing this problem with a new dongle, but all is well, both the load of the bootloader followed by the OTA update work as expected.
Pretty hard to debug when you cannot see the problem!
Perhaps there some user error on his part, but I can't imagine what....
Very odd that the flash of the wireless remote worked well though.....
I told him to wait for a new release, but I expect he will have the same problem.
I am at a loss, do either of you have any ideas?

casainho, 2021-02-27:
See the forum, seems that Windows instructions is missing the mass erase command!!

stsdc, 2021-02-27:
There is possibility to open Discussion tab on any repo.

rananna, 2021-02-28:
From forum results, it's pretty clear that openocd for windows has an outstanding mass_erase problem.
I will raise a new issue.

4var1, 2021-03-01:
> From forum results, it's pretty clear that openocd for windows has an outstanding mass_erase problem.
> I will raise a new issue.

I got a bit lost in all the replies - but doesn't everything work fine with 5v connected?

4var1, 2021-03-01:
@casainho i saw your reply about down assist looking red+green. I'm really surprised you don't see that as yellow. Unless it's different on the controller - to me it looks totally fine. If i blink fast or move my eyes you can see a red flash occasionally - but otherwise the mixing is good.

rananna, 2021-03-01:
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

Indeed. there was far too much back and forth on that topic. He never got it working with windows. The linux build was what gave him the successful flash. I asked him to update his stlink as I read on other forums that mass erase may not work with older firmware.

rananna, 2021-03-01:
> @casainho i saw your reply about down assist looking red+green. I'm really surprised you don't see that as yellow. Unless it's different on the controller - to me it looks totally fine. If i blink fast or move my eyes you can see a red flash occasionally - but otherwise the mixing is good.

IMO, the PWM brightness has a big affect on mixing low brightness does not mix as well. However, I am not too fussed by the appearance. I find it OK, but this is definitely in the personal preference category.

4var1, 2021-03-01:
> > @casainho i saw your reply about down assist looking red+green. I'm really surprised you don't see that as yellow. Unless it's different on the controller - to me it looks totally fine. If i blink fast or move my eyes you can see a red flash occasionally - but otherwise the mixing is good.
>
> IMO, the PWM brightness has a big affect on mixing low brightness does not mix as well. However, I am not too fussed by the appearance. I find it OK, but this is definitely in the personal preference category.

Yea - the only time i've had an issue was when I had a restricted view of the led - so one colour wasn't visible -then it really doesn't mix. That was slightly confusing - but I do think that when a lense/clear silicone or similar is placed over it it will look better too.

To me doesn't make sense that up/down result in the same response. I know it's marginal - but i think any extra positive feedback is always good...

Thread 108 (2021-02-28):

openocd for windows mass_erase not working

rananna, 2021-02-28:
We need a fix for openocd for windows.
Mass_erase is not working and it is needed for the s340 softdevice.

4var1, 2021-03-02:
i don't understand - it works fine.  I do it all the time - is in the openocd.cfg i posted.

I took this reply from filippods to mean it works all ways when powered with 5v...

Sorry, i've accidentally renamed it, now WORKS (**Verify OK**) :i've flashed bootloader with openocd (and openocd.cfg)... The nrf52 must be powered on with 5v, in fact when i power on with 3.3v i can't flash with openocd.cfg in the folder.

rananna, 2021-03-02:
Yes, he had correct verification many times under windows, but the boot loader would not flash. Go down two more posts:

"OK, now what happens when you flash the 0.6.2 firmware using the bootloader?
(keep the board powered with 5V.)

The leds still not blinking and the device not appear in bt list"

And then another post just under that:
"I've completed the linux procedure, now all works fine, i can connect to TSDZ2."

He can flash successfully under Linux.

Anyway, he has gone silent. Maybe nobody else will have these issues with windows.

4var1, 2021-03-02:
Ok - i think we see who else has issues, if anyone. I did the original bootloader flash and OTA update fine from Windows.

rananna, 2021-03-02:
I will keep the issue open for now.
I read on other forums that out of date stlink firmware can cause an issue with mass_erase under windows.
Maybe that was his issue?
Anyway, I just posted a question for you on the forum - could you please have a look?

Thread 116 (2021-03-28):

timing loop that fires too often?

4var1, 2021-03-28:
I was browsing the code - and spotted what I think is another buggy loop timer - is the same construct as was being used in the main loop that caused it to run a lot faster than expected as if the timer resolution is high enough - the mod test will be true for many cycles rather than just one. I'll take a closer look when I have more time...

static void main_timer_timeout(void *p_context)
{
  UNUSED_PARAMETER(p_context);

  main_ticks++;

  if (main_ticks % (1000 / MSEC_PER_TICK) == 0)
    ui32_seconds_since_startup++;

  if ((main_ticks % (50 / MSEC_PER_TICK) == 0) && // every 50ms
      m_rt_processing_stop == false)
    rt_processing();
}

casainho, 2021-03-28:
We need to use APP_TIMERS as is being done on the wireless remote and we would use an APP_TIMER to fire up every 50ms.

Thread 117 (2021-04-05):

Wireless remote STL file error: lower_part.stl has a glitchy floor

rdancer, 2021-04-05:
### Affected documentation page

https://opensourceebike.github.io/remote/build_remote.html

### Affected file

https://opensourceebike.github.io/remote/lower_part.stl

### Expected behaviour

part should look like the rendering:

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.

### Actual behaviour

Part is missing the floor, or rather depending on the editor/viewer, the floor is either missing, or glitchy, or visible as solid only when viewed from below with camera looking upwards.

Some parts of the screw shafts are also missing in OS X Preview, for what that's worth (but the actual 3D printing software is more important.

#### Tested with

##### Merialise Magics

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

##### TinkerCAD.com

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

##### OS X Preview

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

Closed 2021-04-05.

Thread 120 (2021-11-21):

Link to latest docs show display instead of wireless TSDZ2 project

stsdc, 2021-11-21:
Right now it is very hard or impossible to find scheme for connecting nrf52 to TSDZ2. A lot of links are 404.

casainho, 2021-11-21:
Sorry, I need to work on that. What are you looking for? To the display or to the TSDZ2 wireless??

weldinpatt, 2021-11-21:
My interest lies with the TSDZ2 wireless project. Thank you. Casainho , Your work is amazing .

Get Outlook for iOS<https://aka.ms/o0ukef>
________________________________
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

casainho, 2021-11-21:
I kind of achieved the documentation for the TSDZ2 wireless, see it here: https://github.com/OpenSourceEBike/OpenSourceEBike.github.io/blob/main/tsdz2_wireless/index.md

I wrote at bottom of the main page a link to TSDZ2 wireless documentation.

Can you please explain what you like on TSDZ2 wireless? how you will use it? will you build the fully wireless remote or use the wired remote?

stsdc, 2021-11-22:
I'm interested in building Wireless TSDZ2. All those displays are too bulky (except sw102) so it makes sense to just use my phone or optionally a remote.

I managed to flash and solder Wireless TSDZ2, however, I  probably burnt my nrf52. Used converter is  a DD8024TA. Voltage IN 51V, OUT 5V connected to vbus. And nrf52 immediately heats :(

So I ended up buying a new SW102, I'll upload @anszom's firmware. Would be cool to make SW102 to work with an app.

casainho, 2021-11-22:
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

I can't imagine why NRF52 board did burn, all seems ok - well, only that it should not be placed on top of conductive pads as you seem did it.

Ok, the OpenSource display is simultaneously the TSDZ2 wireless + the SW102.

stsdc, 2021-11-22:
@casainho I did insulate nrf52 with a tape.

casainho, 2021-11-22:
Ok, good. So, if you flashed the bootloader with the STLinkV2 and power up the biard with it, that should not happen with the DD8024TA dc-dc.
I now recomend to the display to first flash the bootloader with STLinkV2 powe up the board, then solder only the DC-DC and test with a multimeter the 5V output and only after connect to the NRF52 board.

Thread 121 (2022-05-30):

LEV protocol documentation?

geeksville, 2022-05-30:
Hi @Casainho,

Long time no see!  I hope all is well for you.

My ebike recumbent (based on your project with an old version of our display code) is still happily riding along.  But I'm thinking about buying a Specialized Turbo Vado SL 5.0.  Alas, my preferred bike computer (Hammerhead Karoo 2) doesn't yet support the ANT+ LEV profile.  But they do have a plug-in architecture, so I'm thinking about [writing](https://github.com/hammerheadnav/karoo-sdk/issues/7) a LEV profile plugin.

Googling led me to your new project.  Have you had any luck finding (or reverse engineering) the ANT+ profile.  If so, I'd love to crib from your work.  Of course I'm happy to share anything that might be useful from this plugin I might be making ;-).

Kevin

geeksville, 2022-05-30:
oops - I'm still happy to work together but no need to link me the profile docs.  Found them on the ANT site.

casainho, 2022-05-30:
Hi Kevin!! Nice to see you again.

Garmin is much better on supporting custom apps, with the same development for watches and the GPS cycling computers. If Hammerhead Karoo can't help you, you can consider the Garmin devices.

Yes, the ANT docs are on their site but if you need something, just ask me.

I just built my EBike with a carbon frame and with a Bafang motor M500 (M510 new version weights 3kgs). We can buy the motor parts at unit, and they are not to much expensive. So for a more open system, this is the best motor I could find and Bafang have some good motors, including one M800 that weights 2.3kgs.
We have a LOT of technical knowledge for this motors, they communicate with CAN to the display, torque sensor and battery pack.

The yellow is a mini cargo bike with TSDZ2 and the other is my new one with this motor:
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

And our EasyDIY display, using NRF52840 board + 1.3 inches OLED display + CAN module, running the firmware you developed!!!!

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

geeksville, 2022-05-30:
Super cool.  I'll look into that bafang motor and possibly go that way rather than the Specialized SL 1.1 motor.  Yeah I really like Garmin also (longtime fanboy) and I still have my Fenix 6.  But I sold my edge 830 because OMG (except for missing ebike support) I was **way** more impressed with the Karoo.  It is so fast and the maps/nav is so nice also the screen is amazing.  I'm reluctant to give that up so I'm investigating using their SDK to write a plugin for their GUI (their device runs android).

casainho, 2022-05-30:
I did my build based on this build guide - the same frame and almost the same components: https://www.emtbforums.com/community/threads/my-dengfu-e10-build.24436
Note that currently you can use the new M510 that is 3kg instead of M500 that is 3.6kg.

I had the Fenix 6 and bought the Fenix 7 mainly because of stamina feature.
I do some light trail runs and I use a Garmin watch that has a metric called "stamina" that represents my energy. As I am tall, fat and not fit, I have low stamina and so I need to manage very well my energy so I can go to the end of the trails of 15kms.
For example today, I was able to run the 15 kms and never stop to walk because I was tired, so I did manage well my energy and in the end, my Garmin watch stamina said I had energy for only more 3kms - quite accurate for the way I was felling tired:

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

The Garmin watches or cycling GPS computers as Edge, can also calculate stamina for cycling activities but for that it needs the real time input of pedal human power. My plan is to calculate the pedal human power from Bafang M500/M600 torque sensor, using our EasyDIY display, and send wireless by ANT to the watch or GPS computer, so the user will be able to see later the graph of pedal human power as also got the real time stamina while cycling.

Here the example of my running power (around average 250W) and stamina graphs on the 15 kms trail run - I use the Stryd run power meter:

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

I have high expectations for doing more fitness with this new EBike, and so I wish to also keep managing my own energy and not only the battery energy :)

geeksville, 2022-05-31:
oh yes - one of my reasons for going for the specialized is (currently)
options for ebikes with integrated ANT+ Power meter are limited ;-).  I
totally agree that adding Power broadcasts from an open source motor system
would be super great!

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

geeksville, 2022-06-01:
re your mountain bike (if you don't mind me cluttering github with these questions ;-)):

I don't suppose you've run across a slick carbon street/hybrid frame that is M510 compatible?  I might try doing your same DIY thing (and using/participating in your project again - heh) instead of specialized.  In short: I'm looking for lightweight, small battery small motor - kinda a "regular bike but with a bit of eassist" .  Something kinda like https://www.specialized.com/us/en/turbo-vado-sl-5-0-eq/p/188200?color=319600-188200

Any thoughts @casainho ?

casainho, 2022-06-01:
Maybe this: Dengfu and Lightcarbon have frames for road bikes, for Bafang M800 (2.3 kg, 200W motor).

This companies do not build for us, it is for OEM. We are lucky that they are available to sell to us at unit. Like many others, I contacted by e-mail [Melody <tony@dengfubikes.com>], got all details by e-mail and paid to their PayPal. I also got e-mail contact with [Jim Lee <jim@lightcarbon.com>] but I ended up to buy instead the Dengfu E10 frame - note that sometimes they do not even have listed their new frames on their sites, so you need to ask!!

M800 will be more difficult to find the parts but again, I think you need to ask to shops like GreenBikeKit and they will probably get it to you.

The frame is probably the hard part to find. After the motor, but currently, with shops selling the motor including all parts for maintenance, that is easy!! Then the battery can be done by yourself or buy to the frame seller (Dengfu sells the battery pack or only the empty box). The other mechanical bike parts, very easy, I am not a mechanical engineer but seem to me that parts are very easy to assembly, just like Ikea - I just bought a torque wrench and did follow torque tables for screws, for MTB.

M510 or M800, seems they are the best motors we can find for DIY. One one youtube review from a experienced guy testing EBike motors, he says M500 is one of the silent motors he tried. So, a motor that is silent, light, and that we can DIY build our EBike including customizing our battery pack (battery pack is not locked to the motor), and developing our own firmware - this is the best we can get!!!

For the first time ever, I decided to build my own battery, and with that popular advanced BMS with Bluetooth, and I bought the cells from an well know EU shop: https://www.nkon.nl

So I were able to optimize my battery pack characteristics, choosing the best cells for my usage, weight / current discharge / capacity / internal resistance. And our EasyDIY display calculate the battery pack resistance and in future I want to more careful look at it since both capacity degradation and battery resistance, are the indicators for battery age.

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

geeksville, 2022-06-01:
ooh that's super useful.  I'll do some investigation and try to find a frame that fits my usecase.  Thank you for the great photos also.

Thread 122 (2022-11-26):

REQ: External temp sensor AND still be able to use the throttle

rayholland, 2022-11-26:
Would it be possible to extend the nRF52840 firmware code to attach a temp sensor to a free nRF52840 ADC pin and read the motor temp?
And in the app have an option to set the warning and shutdown temp thresholds?

The nRF52840 then starts updating the controller Max Current and Max Power when the warning threshold is crossed, down to 0 when the temperature reaches the shutoff threshold (linear scale). Same as the TSDZ2-ESP32 does (https://github.com/TSDZ2-ESP32/TSDZ2-ESP32-Wiki/wiki/Optional-Temperature-sensor)

This way we could use a throttle and still have motor temp overheating protection.

weldinpatt, 2022-11-26:
Run a separate wire to your heat detecting kit may be a buck too. Are you doing the wireless project?

Sent from Outlook for iOS<https://aka.ms/o0ukef>
________________________________
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

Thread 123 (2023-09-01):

Garmin data fields not found

sharkillator, 2023-09-01:
Hi,

I would like to get data on my Fenix 7. I edited setup file to declare Fenix7 as compatible device, build the app and put the prg in /Garmin/Apps on my watch.
I can connect to the bike via ant+ without any problem but I can not add data fields. Only field Motor Power is present and not updated with current motor power value.
Could you help me ?
Thanks for this great work !

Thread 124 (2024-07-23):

cannot flash the norsik dongle and need help

joda2102, 2024-07-23:
I have a tsdz2 motor and found this project for a wireless solution.
I bought a nRF52840 Nordic USB Dongle cabeled it as discribed in
https://opensourceebike.github.io/easy_diy_display_ebike_display/tsdz2_wireless/getting_started.html
to a stlink-v2 and followed the instruction
https://opensourceebike.github.io/easy_diy_display_ebike_display/tsdz2_wireless/windows.html

flashing failed

output was
PS C:\Users\joerg\github\openocd\bin> ./openocd.exe -f ../share/openocd/scripts/interface/stlink.cfg -f ../share/openocd/scripts/target/nrf52.cfg -c "program TSDZ2_wireless-bootloader_with_sd-v0.9.0.hex verify" -c "exit"
Open On-Chip Debugger 0.12.0 (2023-10-02) [https://github.com/sysprogs/openocd]
Licensed under GNU GPL v2
libusb1 09e75e98b4d9ea7909e8837b7a3f00dda4589dc3
For bug reports, read
        http://openocd.org/doc/doxygen/bugs.html
Info : auto-selecting first available session transport "hla_swd". To override use 'transport select <transport>'.
Info : The selected transport took over low-level target control. The results might differ compared to plain JTAG/SWD

nRF52 device has a CTRL-AP dedicated to recover the device from AP lock.
A high level adapter (like a ST-Link) you are currently using cannot access
the CTRL-AP so 'nrf52_recover' command will not work.
Do not enable UICR APPROTECT.

Info : clock speed 1000 kHz
Info : STLINK V2J37S7 (API v2) VID:PID 0483:3748
Info : Target voltage: 3.256685
Warn : target nrf52.cpu examination failed
Info : starting gdb server for nrf52.cpu on 3333
Info : Listening on port 3333 for gdb connections
embedded:startup.tcl:1467: Error: ** Unable to reset target **
in procedure 'program'
in procedure 'program_error' called at file "embedded:startup.tcl", line 1504
at file "embedded:startup.tcl", line 1467
PS C:\Users\joerg\github\openocd\bin>

after researching I tried

PS C:\Users\joerg\github\openocd\bin> ./openocd.exe -f ../share/openocd/scripts/interface/stlink.cfg -f ../share/openocd/scripts/target/nrf52.cfg -c "adapter speed 950" -c "init" -c "halt" -c "nrf52.dap apreg 1 0x04 0x01" -c "nrf5 mass_erase" -c "program TSDZ2_wireless-bootloader_with_sd-v0.9.0.hex verify" -c "exit"
Open On-Chip Debugger 0.12.0 (2023-10-02) [https://github.com/sysprogs/openocd]
Licensed under GNU GPL v2
libusb1 09e75e98b4d9ea7909e8837b7a3f00dda4589dc3
For bug reports, read
        http://openocd.org/doc/doxygen/bugs.html
Info : auto-selecting first available session transport "hla_swd". To override use 'transport select <transport>'.
Info : The selected transport took over low-level target control. The results might differ compared to plain JTAG/SWD

nRF52 device has a CTRL-AP dedicated to recover the device from AP lock.
A high level adapter (like a ST-Link) you are currently using cannot access
the CTRL-AP so 'nrf52_recover' command will not work.
Do not enable UICR APPROTECT.

adapter speed: 950 kHz
Info : clock speed 950 kHz
Info : STLINK V2J37S7 (API v2) VID:PID 0483:3748
Info : Target voltage: 3.255080
Warn : target nrf52.cpu examination failed
Info : starting gdb server for nrf52.cpu on 3333
Info : Listening on port 3333 for gdb connections
Error: Target not examined yet

openocd on linux: same issue
I was able to telnet connect via putty localhost 4444.
Open On-Chip Debugger
> init
> halt
Target not examined yet

> nrf52.dap apreg 1 0x04 0x01
nrf52.dap

>

Norsic Tool nrfutil
 nrfutil pkg generate --hw-version 52 --debug-mode --sd-req=0x00  --application TSDZ2_wireless-bootloader_with_sd-v0.9.0.hex --application-version 1 app.zip
 nrfutil dfu usb-serial -pkg app.zip -p COM6
 PS C:\Users\joerg\github\work> nrfutil dfu usb-serial -pkg app.zip -p COM6
  [------------------------------------]    0%
Traceback (most recent call last):
  File "nordicsemi\__main__.py", line 1555, in <module>
  File "click\core.py", line 1137, in __call__
  File "click\core.py", line 1062, in main
  File "click\core.py", line 1668, in invoke
  File "click\core.py", line 1668, in invoke
  File "click\core.py", line 1404, in invoke
  File "click\core.py", line 763, in invoke
  File "nordicsemi\__main__.py", line 1032, in usb_serial
  File "nordicsemi\__main__.py", line 988, in do_serial
  File "nordicsemi\dfu\dfu.py", line 127, in dfu_send_images
  File "nordicsemi\dfu\dfu.py", line 95, in _dfu_send_image
  File "nordicsemi\dfu\dfu_transport_serial.py", line 250, in send_init_packet
  File "nordicsemi\dfu\dfu_transport_serial.py", line 244, in try_to_recover
  File "nordicsemi\dfu\dfu_transport_serial.py", line 421, in __execute
  File "nordicsemi\dfu\dfu_transport_serial.py", line 504, in __get_response
pc_ble_driver_py.exceptions.NordicSemiException: Response Code InsufficientResources
[15196] Failed to execute script '__main__' due to unhandled exception!
PS C:\Users\joerg\github\work>

Can anyone help?

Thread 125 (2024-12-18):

TSDZ2B has bluetooth built in?

tung256, 2024-12-18:
TSDZ2B has bluetooth??? it shows up on my devices but i have no idea which app i can use to connect to it.
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

after googling, i think i found the app but it is definitely not compatible.
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

which app will work?

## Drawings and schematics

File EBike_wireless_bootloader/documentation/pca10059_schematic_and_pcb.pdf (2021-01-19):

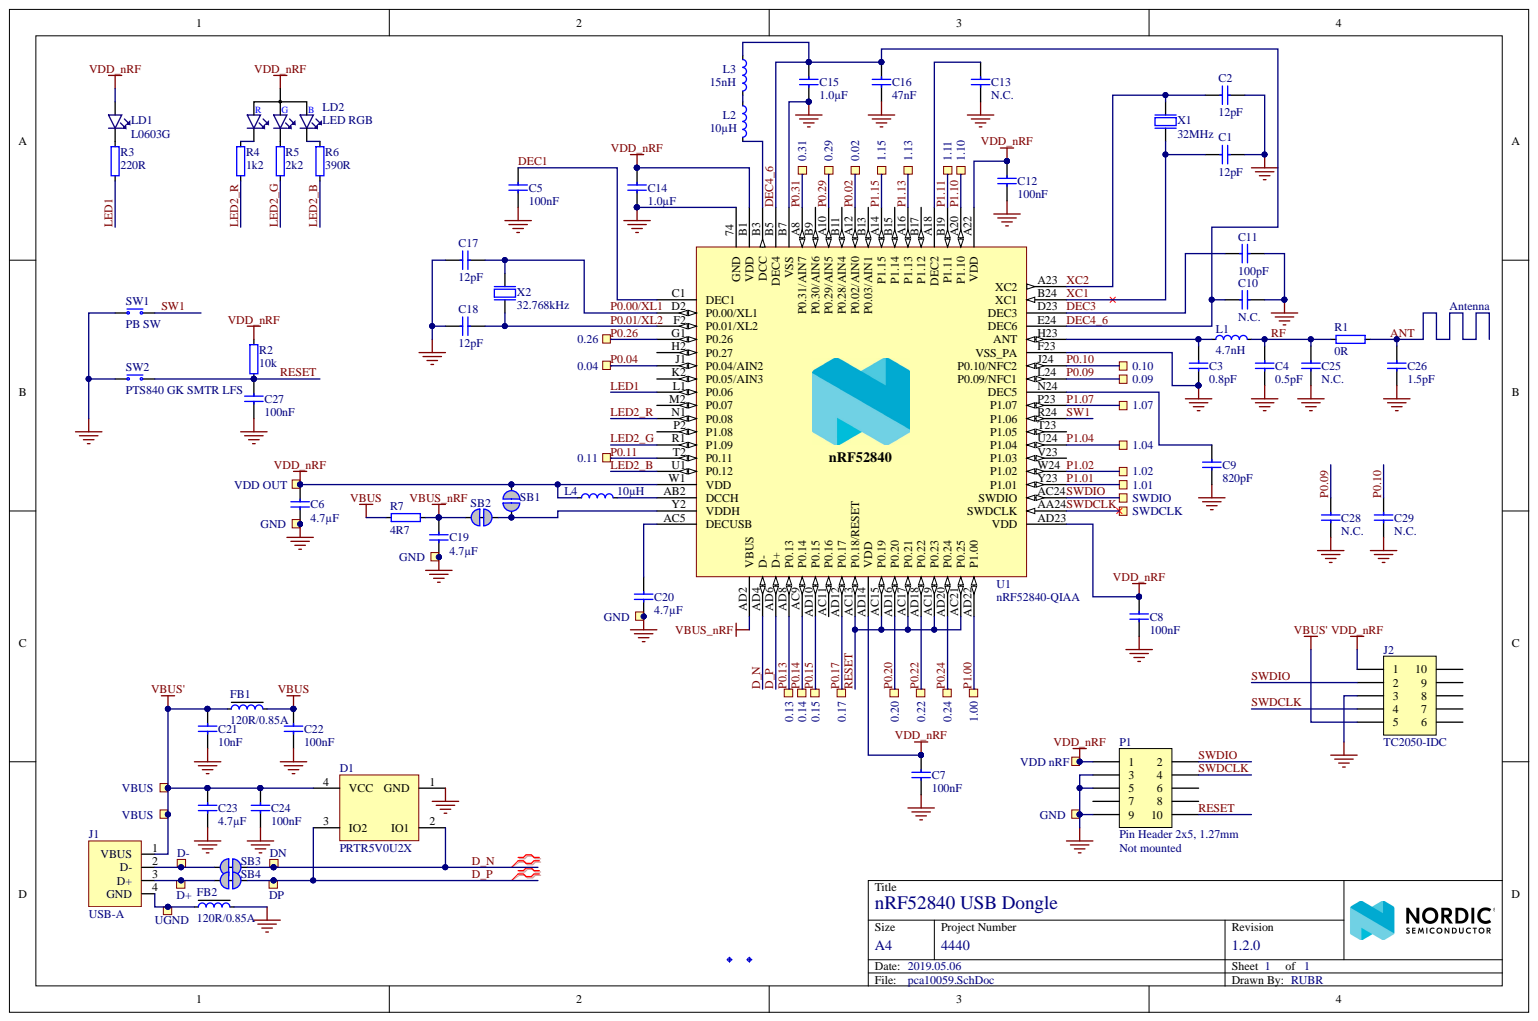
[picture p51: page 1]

X2
32.768kHz | | P0.00/XL1 D2 | DEC3

P0.01/XL2 | | DEC4_6

VDDH Y2 DCCH AB2

DECUSB AC5

Title nRF52840 USB Dongle

Size A4 | Project Number 4440 | Revision 1.2.0

Date: 2019.05.06 | Sheet 1 of 1
File: pca10059.SchDoc | Drawn By: RUBR

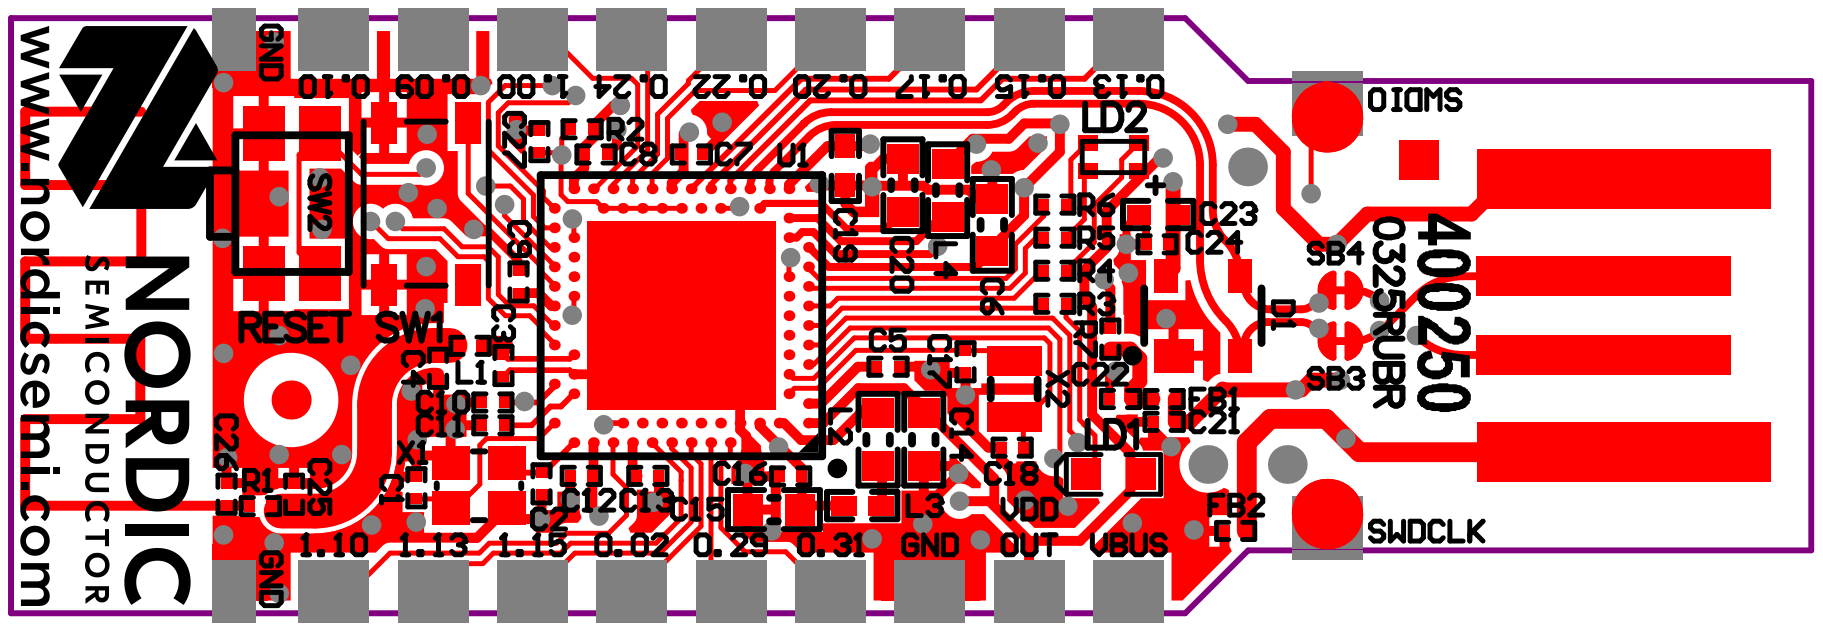
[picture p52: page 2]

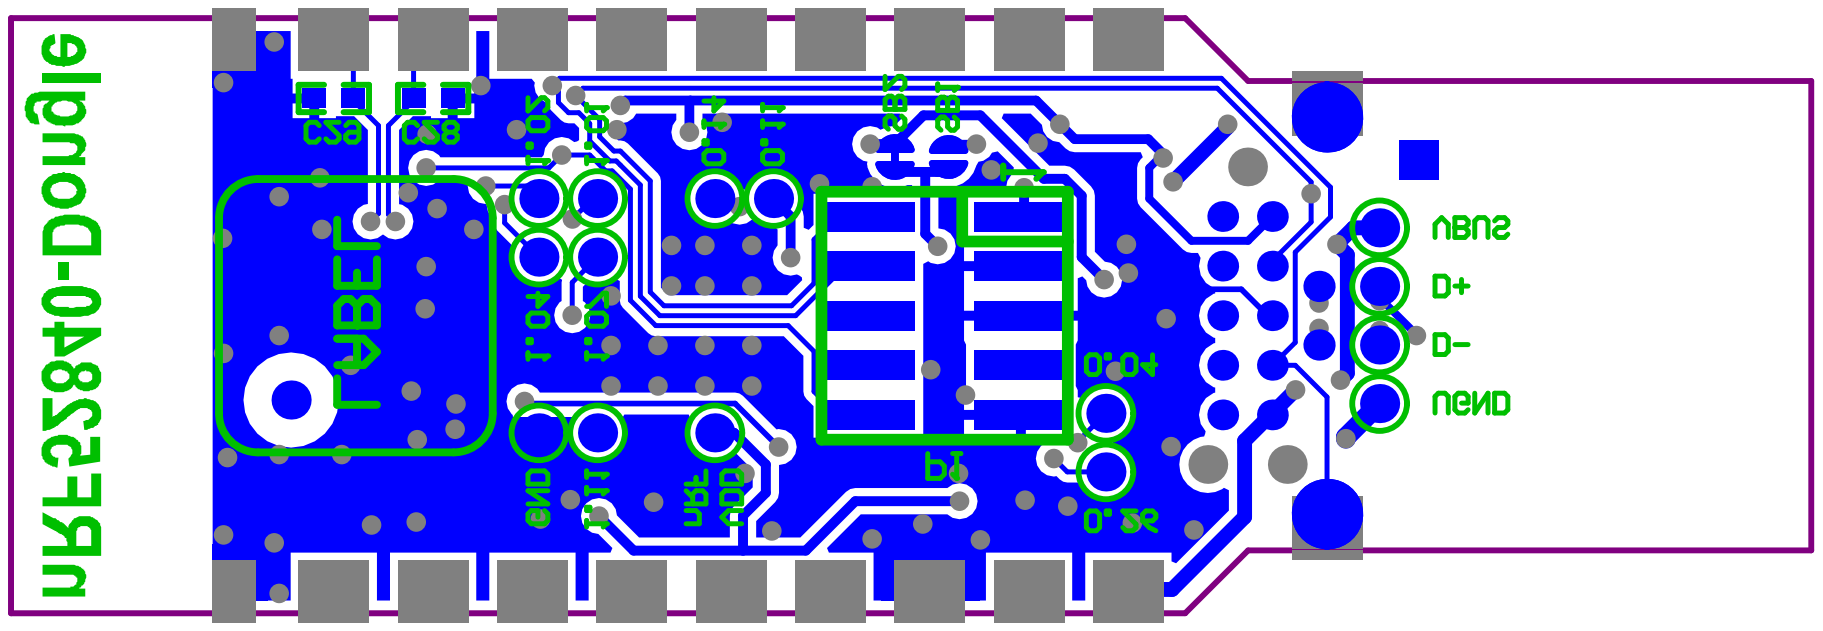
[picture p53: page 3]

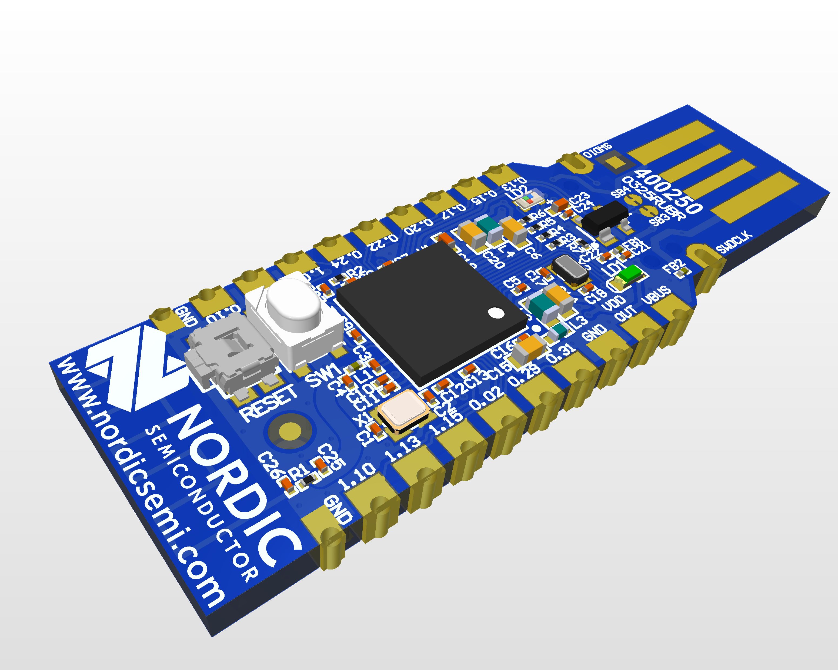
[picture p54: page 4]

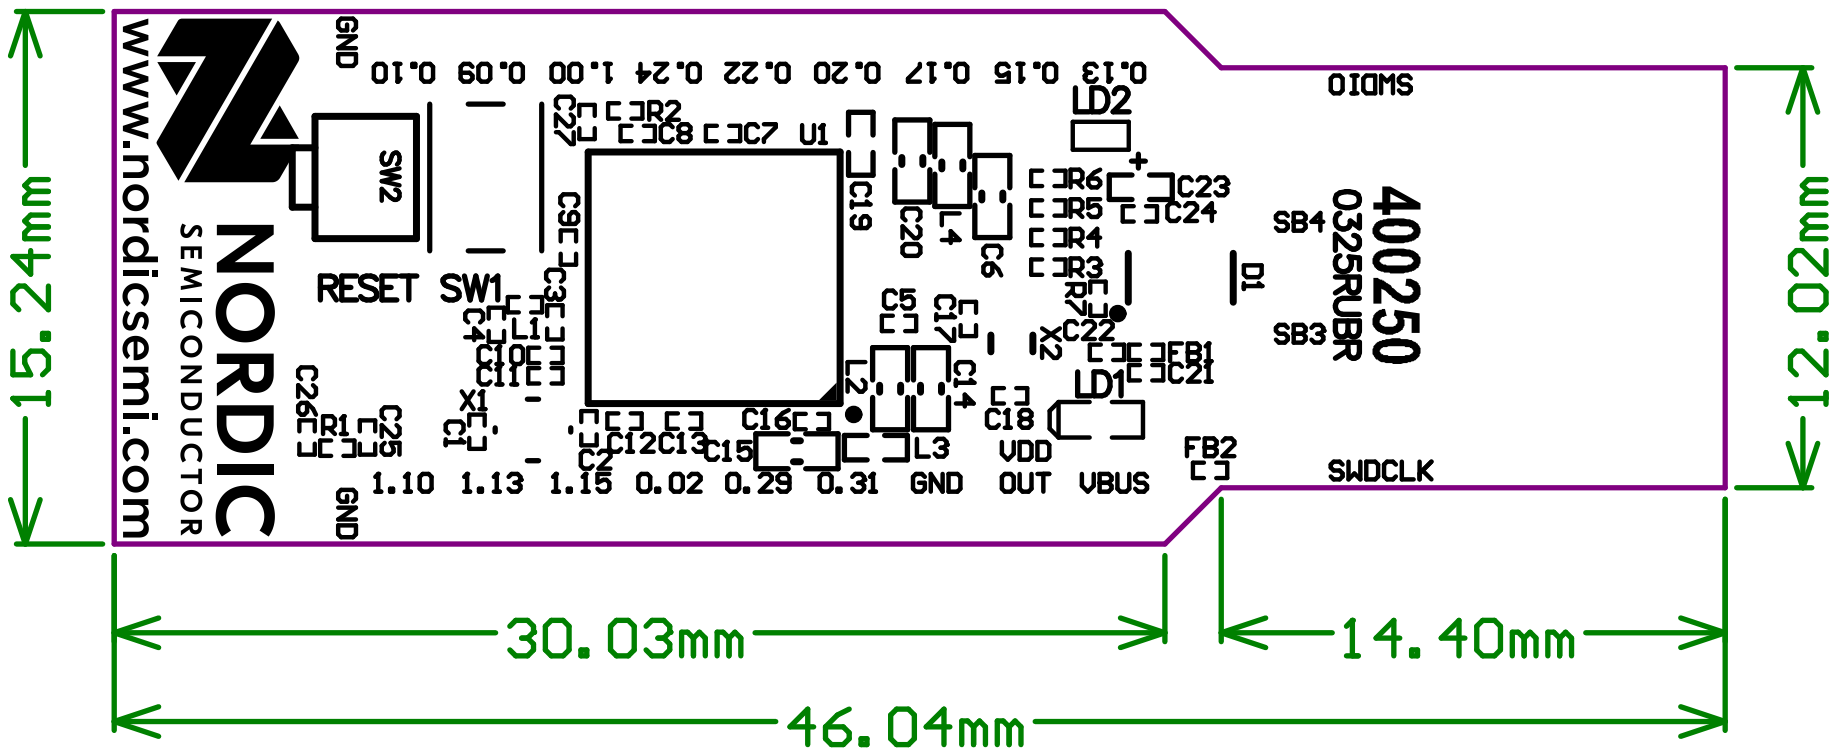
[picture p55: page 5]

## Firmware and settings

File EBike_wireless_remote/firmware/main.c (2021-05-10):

/*
 * TSDZ2 EBike wireless remote firmware
 *
 * Copyright (C) Casainho, 2020
 * Copyright (C) Rananna, 2020
 *
 * Released under the GPL License, Version 3
 */

#include <stdio.h>
#include <stdint.h>
#include "app_timer.h"
#include "nrf_pwr_mgmt.h"
#include "nrf_sdh.h"
#include "ble.h"
#include "ble_err.h"
#include "ble_hci.h"
#include "ble_srv_common.h"
#include "ble_advdata.h"
#include "ble_conn_params.h"
#include "ble_conn_state.h"
#include "peer_manager.h"
#include "peer_manager_handler.h"
#include "ble_advdata.h"
#include "ble_advertising.h"
#include "nrf_sdh.h"
#include "nrf_sdh_ble.h"
#include "nrf_ble_gatt.h"
#include "nrf_ble_qwr.h"
#include "ble_services.h"
#include "nrf_sdh_ant.h"
#include "ant_key_manager.h"
#include "ant_lev.h"
#include "pins.h"
#include "app_util_platform.h"
#include "ant_interface.h"
#include "nrf_delay.h"
#include "fds.h"

#include "app_button.h"
#include "nrf_drv_clock.h"
#include "sdk_config.h"
#include "ant_state_indicator.h"
#include "bsp_btn_ant.h"
#include "antplus_controls.h"
#include "eeprom.h"
#include "nrf_sdh_soc.h"
#include "nrf_power.h"
#include "nrf_bootloader_info.h"
#include "nrf_gpio.h"
#include "bsp.h"
#include "nrf_log.h"
#include "nrf_log_ctrl.h"
#include "nrf_drv_gpiote.h"
#include "common.h"
#include "ledalert.h"
#include "nordic_common.h"

#include "ant_search_config.h"
#include <math.h>
#define WAIT_TIME 1000 // wait 3 seconds before a reset
bool config_press = false;
//motor state control variables
uint8_t motor_init_state = 0;
uint8_t motor_error_state;
uint8_t motor_soc_state;
bool motor_display_soc = false;
bool display_assist = false;
uint8_t walk_mode = 0;
uint8_t light_mode = 0;
bool disp_config_flag = false;

bool searching_flag = false;

#define BUTTON_DETECTION_DELAY APP_TIMER_TICKS(10)           /**< Delay from a GPIOTE event until a button is reported as pushed (in number of timer ticks). */
#define BUTTON_PRESS_TIMEOUT APP_TIMER_TICKS(60 * 60 * 1000) // 1h to enter low power mode
#define BUTTON_LONG_PRESS_TIMEOUT APP_TIMER_TICKS(1000)      // 1 seconds for long press
#define BUTTON_CONFIG_PRESS_TIMEOUT APP_TIMER_TICKS(5000)    // 5 seconds TO ENTER CONFIG MODE

#define ANT_Search_TIMEOUT APP_TIMER_TICKS(600) // 600 ms for Ant Search check
#define DEVICE_NAME "TSDZ2_remote"              /**< Name of device. Will be included in the advertising data. */

#define APP_BLE_CONN_CFG_TAG 1 /**< A tag identifying the SoftDevice BLE configuration. */

#define APP_ADV_INTERVAL 64                                    /**< The advertising interval (in units of 0.625 ms; this value corresponds to 40 ms). */
#define APP_ADV_DURATION BLE_GAP_ADV_TIMEOUT_GENERAL_UNLIMITED /**< The advertising time-out (in units of seconds). When set to 0, we will never time out. */

#define MIN_CONN_INTERVAL MSEC_TO_UNITS(100, UNIT_1_25_MS) /**< Minimum acceptable connection interval (0.5 seconds). */
#define MAX_CONN_INTERVAL MSEC_TO_UNITS(200, UNIT_1_25_MS) /**< Maximum acceptable connection interval (1 second). */
#define SLAVE_LATENCY 0                                    /**< Slave latency. */
#define CONN_SUP_TIMEOUT MSEC_TO_UNITS(4000, UNIT_10_MS)   /**< Connection supervisory time-out (4 seconds). */

#define FIRST_CONN_PARAMS_UPDATE_DELAY APP_TIMER_TICKS(20000) /**< Time from initiating event (connect or start of notification) to first time sd_ble_gap_conn_param_update is called (15 seconds). */
#define NEXT_CONN_PARAMS_UPDATE_DELAY APP_TIMER_TICKS(5000)   /**< Time between each call to sd_ble_gap_conn_param_update after the first call (5 seconds). */
#define MAX_CONN_PARAMS_UPDATE_COUNT 3                        /**< Number of attempts before giving up the connection parameter negotiation. */

#define SEC_PARAM_BOND 1                               /**< Perform bonding. */
#define SEC_PARAM_MITM 0                               /**< Man In The Middle protection not required. */
#define SEC_PARAM_LESC 0                               /**< LE Secure Connections not enabled. */
#define SEC_PARAM_KEYPRESS 0                           /**< Keypress notifications not enabled. */
#define SEC_PARAM_IO_CAPABILITIES BLE_GAP_IO_CAPS_NONE /**< No I/O capabilities. */
#define SEC_PARAM_OOB 0                                /**< Out Of Band data not available. */
#define SEC_PARAM_MIN_KEY_SIZE 7                       /**< Minimum encryption key size. */
#define SEC_PARAM_MAX_KEY_SIZE 16                      /**< Maximum encryption key size. */

#define APP_FEATURE_NOT_SUPPORTED BLE_GATT_STATUS_ATTERR_APP_BEGIN + 2 /**< Reply when unsupported features are requested. */

#define CONTROLS_HW_REVISION 2
#define LEV_HW_REVISION 1

#define CONTROLS_MANUFACTURER_ID 255
#define LEV_MANUFACTURER_ID 254

#define CONTROLS_MODEL_NUMBER 2
#define LEV_MODEL_NUMBER 1

#define CONTROLS_SW_REVISION_MAJOR 2
#define LEV_SW_REVISION_MAJOR 1

#define CONTROLS_SW_REVISION_MINOR 2
#define LEV_SW_REVISION_MINOR 1

#define CONTROLS_SERIAL_NUMBER 3241
#define LEV_SERIAL_NUMBER 1234

#define CONTROLS_CHANNEL_NUM 1 //see: NRF_SDH_ANT_TOTAL_CHANNELS_ALLOCATED in sdk_config.sys
#define LEV_CHANNEL_NUM 0      //LEV on chan 0,CONTROL on chan 1

#define ANT_LEV_ANT_OBSERVER_PRIO 1
#define ANT_CONTROLS_ANT_OBSERVER_PRIO 1

#define CONTROLS_CHAN_ID_TRANS_TYPE 0 // slave wildcard match
#define LEV_CHAN_ID_TRANS_TYPE 0

#define CONTROLS_CHAN_ID_DEV_NUM 0 // wildcard match to any master
#define LEV_CHAN_ID_DEV_NUM 0

#define ANTPLUS_NETWORK_NUM 0

// @snippet [ANT LEV RX Instance]
void ant_lev_evt_handler(ant_lev_profile_t *p_profile, ant_lev_evt_t event);
void antplus_controls_evt_handler(antplus_controls_profile_t *p_profile, antplus_controls_evt_t event);

LEV_DISP_CHANNEL_CONFIG_DEF(m_ant_lev,
                            LEV_CHANNEL_NUM,
                            LEV_CHAN_ID_TRANS_TYPE,
                            LEV_CHAN_ID_DEV_NUM,
                            ANTPLUS_NETWORK_NUM,
                            LEV_MSG_PERIOD_4Hz);

CONTROLS_SENS_CHANNEL_CONFIG_DEF(m_antplus_controls,
                                 CONTROLS_CHANNEL_NUM,
                                 CONTROLS_CHAN_ID_TRANS_TYPE,
                                 CONTROLS_CHAN_ID_DEV_NUM,
                                 ANTPLUS_NETWORK_NUM,
                                 CONTROLS_MSG_PERIOD_4Hz);

CONTROLS_SENS_PROFILE_CONFIG_DEF(m_antplus_controls,
                                 antplus_controls_evt_handler);

static ant_lev_profile_t m_ant_lev;
static antplus_controls_profile_t m_antplus_controls;

NRF_SDH_ANT_OBSERVER(m_ant_observer, ANT_LEV_ANT_OBSERVER_PRIO, ant_lev_disp_evt_handler, &m_ant_lev);
NRF_SDH_ANT_OBSERVER(m_ant_observer_control, ANT_CONTROLS_ANT_OBSERVER_PRIO, antplus_controls_sens_evt_handler, &m_antplus_controls);
uint8_t configuration_flag = 0;     // flag to determine configutaion mode 1 config mode/ 0 normal mode
bool enable_configuration = false;  //used to turn on config mode
bool disable_configuration = false; //used to turn off config mode

uint8_t ebike = 1;  //ebike control as default                                                //ANT LEV ebike as a default
uint8_t garmin = 0; //no garmin computer as a default
uint8_t brake = 0;  //BRAKE FLAG
bool m_button_long_press = false;
bool shutdown_flag = false;
bool brightness_flag = false;
NRF_BLE_GATT_DEF(m_gatt);           /**< GATT module instance. */
NRF_BLE_QWR_DEF(m_qwr);             /**< Context for the Queued Write module.*/
BLE_ADVERTISING_DEF(m_advertising); /**< Advertising module instance. */
BLE_ANT_ID_DEF(m_ble_ant_id_service);
//test flash write completed
static uint16_t m_conn_handle = BLE_CONN_HANDLE_INVALID; /**< Handle of the current connection. */
//static uint8_t m_adv_handle = BLE_GAP_ADV_SET_HANDLE_NOT_SET;           /**< Advertising handle used to identify an advertising set. */
//static uint8_t m_enc_advdata[BLE_GAP_ADV_SET_DATA_SIZE_MAX];            /**< Buffer for storing an encoded advertising set. */
//static uint8_t m_enc_scan_response_data[BLE_GAP_ADV_SET_DATA_SIZE_MAX]; /**< Buffer for storing an encoded scan data. */

uint8_t old_ant_device_id = 0; // initially in pairing mode
uint8_t new_ant_device_id = 0; // used to check for change of ant id

/**@brief Struct that contains pointers to the encoded advertising data. */
/*
static ble_gap_adv_data_t m_adv_data =
    {
        .adv_data =
            {
                .p_data = m_enc_advdata,
                .len = BLE_GAP_ADV_SET_DATA_SIZE_MAX},
        .scan_rsp_data =
            {
                .p_data = m_enc_scan_response_data,
                .len = BLE_GAP_ADV_SET_DATA_SIZE_MAX}};
*/

APP_TIMER_DEF(ANT_Search_timer);
APP_TIMER_DEF(multiple_click_timer);
#define CLICK_INTERVAL APP_TIMER_TICKS(250) // count # of button clicks in 0.25 seconds
uint8_t button_clicks = 0;
bool enter_pin_flag = false;
bool standby_pin_flag = false;

static void multiple_click_timeout(void *p_context)
{
  UNUSED_PARAMETER(p_context);
  //process button clicks

  if (button_clicks >= 2) //more than one click
  {
    if ((standby_pin_flag) && (motor_init_state == 0))
      shutdown_flag = true; // set flag for low power

    if (enter_pin_flag)
      brightness_flag = true; // change brightness
  }
  //reset button clicks and flags
  enter_pin_flag = false;
  standby_pin_flag = false;
  button_clicks = 0;
}

void check_motor_init()
{
  static bool soc_disp = true;

  static bool motor_on;
  //static bool key_disp = false;

  //display SOC if standby key pressed and motor is on
  // if (motor_display_soc && motor_soc_state && key_disp && (motor_init_state == 1)) // display soc when STANDBY Key is pressed
  if (motor_display_soc && motor_init_state == 1) // display soc when STANDBY Key is pressed
  {
    disp_soc(motor_soc_state);
    motor_display_soc = false;
  }

  switch (motor_init_state)
  {
  case 0: //motor off
    if (motor_on)
    {
      {
        nrf_lp_delay_ms(500);
        led_sequence_play_next(LED_EVENT_MOTOR_OFF);
        motor_on = false;
        // disp_soc(motor_soc_state);
      }
    }
    //key_disp = false;

    break;
  case 1: //motor on

    if (soc_disp && motor_soc_state) //display if soc>0
    {
      ////indicate the motor SOC when motor turns on
      if (!searching_flag) //needed if you have a garmin bike computer
      {
        led_sequence_play_next(LED_EVENT_MOTOR_ON_COMPLETE);
      }
      motor_on = true;
      soc_disp = false;
      // key_disp = true;
    }
    break;
  case 2: //motor initializing
    nrf_lp_delay_ms(500);
    led_sequence_play(LED_EVENT_MOTOR_ON_WAIT);
    soc_disp = true; //show the soc when motor turns on

    break;
  case 3: //used to signal turning  motor on/off
    // do nothing

    break;
  }
  //check for motor errors

  switch (motor_error_state)
  {
  case 1: //MOTOR_INIT_ERROR_ALIVE:

    break;
  case 2: //MOTOR_INIT_ERROR_GET_FIRMWARE_VERSION
  case 3: //MOTOR_INIT_ERROR_FIRMWARE_VERSION
    break;
  case 4: //MOTOR_INIT_ERROR_SET_CONFIGURATIONS

    break;
  }
}
static ble_uuid_t m_adv_uuids[] = /**< Universally unique service identifiers. */
    {
        {BLE_UUID_HEALTH_THERMOMETER_SERVICE, BLE_UUID_TYPE_BLE},
        {BLE_UUID_BATTERY_SERVICE, BLE_UUID_TYPE_BLE},
        {BLE_UUID_DEVICE_INFORMATION_SERVICE, BLE_UUID_TYPE_BLE}};

/**@brief Clear bond information from persistent storage.
 */

//uint32_t err_code=0;
volatile uint32_t main_ticks;

static void delete_bonds(void)
{
  ret_code_t err_code;

  NRF_LOG_INFO("Erase bonds!");

  err_code = pm_peers_delete();
  APP_ERROR_CHECK(err_code);
}

/**@brief Function for starting advertising.
 */
static void advertising_start(bool erase_bonds)
{
  if (erase_bonds == true)
  {
    delete_bonds();
    // Advertising is started by PM_EVT_PEERS_DELETE_SUCCEEDED event.
  }
  else
  {
    uint32_t err_code = ble_advertising_start(&m_advertising, BLE_ADV_MODE_FAST);
    APP_ERROR_CHECK(err_code);
  }
}

/**@brief Function for handling BLE events.
 *
 * @param[in]   p_ble_evt   Bluetooth stack event.
 * @param[in]   p_context   Unused.
 */
static void ble_evt_handler(ble_evt_t const *p_ble_evt, void *p_context)
{
  ret_code_t err_code;

  switch (p_ble_evt->header.evt_id)
  {
  case BLE_GAP_EVT_CONNECTED:
    NRF_LOG_INFO("Connected");
    m_conn_handle = p_ble_evt->evt.gap_evt.conn_handle;
    err_code = nrf_ble_qwr_conn_handle_assign(&m_qwr, m_conn_handle);
    APP_ERROR_CHECK(err_code);
    break;

  case BLE_GAP_EVT_DISCONNECTED:
    NRF_LOG_INFO("Disconnected");
    m_conn_handle = BLE_CONN_HANDLE_INVALID;
    advertising_start(false);
    break;

  case BLE_GAP_EVT_SEC_PARAMS_REQUEST:
    break;

  case BLE_GAP_EVT_PHY_UPDATE_REQUEST:
  {
    NRF_LOG_DEBUG("PHY update request.");
    ble_gap_phys_t const phys =
        {
            .rx_phys = BLE_GAP_PHY_AUTO,
            .tx_phys = BLE_GAP_PHY_AUTO,
        };
    err_code = sd_ble_gap_phy_update(p_ble_evt->evt.gap_evt.conn_handle, &phys);
    APP_ERROR_CHECK(err_code);
  }
  break;

  case BLE_GATTS_EVT_SYS_ATTR_MISSING:
    // No system attributes have been stored.
    err_code = sd_ble_gatts_sys_attr_set(m_conn_handle, NULL, 0, 0);
    APP_ERROR_CHECK(err_code);
    break;

  case BLE_GATTC_EVT_TIMEOUT:
    // Disconnect on GATT Client timeout event.
    NRF_LOG_DEBUG("GATT Client Timeout.");
    err_code = sd_ble_gap_disconnect(p_ble_evt->evt.gattc_evt.conn_handle,
                                     BLE_HCI_REMOTE_USER_TERMINATED_CONNECTION);
    APP_ERROR_CHECK(err_code);
    break;

  case BLE_GATTS_EVT_TIMEOUT:
    // Disconnect on GATT Server timeout event.
    NRF_LOG_DEBUG("GATT Server Timeout.");
    err_code = sd_ble_gap_disconnect(p_ble_evt->evt.gatts_evt.conn_handle,
                                     BLE_HCI_REMOTE_USER_TERMINATED_CONNECTION);
    APP_ERROR_CHECK(err_code);
    break;

  case BLE_GATTS_EVT_RW_AUTHORIZE_REQUEST:
  {
    ble_gatts_evt_rw_authorize_request_t req;
    ble_gatts_rw_authorize_reply_params_t auth_reply;

    req = p_ble_evt->evt.gatts_evt.params.authorize_request;

    if (req.type != BLE_GATTS_AUTHORIZE_TYPE_INVALID)
    {
      if ((req.request.write.op == BLE_GATTS_OP_PREP_WRITE_REQ) ||
          (req.request.write.op == BLE_GATTS_OP_EXEC_WRITE_REQ_NOW) ||
          (req.request.write.op == BLE_GATTS_OP_EXEC_WRITE_REQ_CANCEL))
      {
        if (req.type == BLE_GATTS_AUTHORIZE_TYPE_WRITE)
        {
          auth_reply.type = BLE_GATTS_AUTHORIZE_TYPE_WRITE;
        }
        else
        {
          auth_reply.type = BLE_GATTS_AUTHORIZE_TYPE_READ;
        }
        auth_reply.params.write.gatt_status = APP_FEATURE_NOT_SUPPORTED;
        sd_ble_gatts_rw_authorize_reply(p_ble_evt->evt.gatts_evt.conn_handle, &auth_reply);
      }
    }
  }
  break; // BLE_GATTS_EVT_RW_AUTHORIZE_REQUEST

  default:
    // No implementation needed.
    break;
  }
}

//APP_TIMER_DEF(m_lev_send);
APP_TIMER_DEF(m_timer_button_press_timeout);
APP_TIMER_DEF(m_timer_button_long_press_timeout);
APP_TIMER_DEF(m_timer_button_config_press_timeout);

//APP_TIMER_DEF(m_antplus_controls_send);

button_pins_t m_buttons_wait_to_send = 0;
bool m_timer_buttons_send_running = false;

//set default  old ant ID for reset;

APP_TIMER_DEF(bluetooth_timer);

#define BLUETOOTH_TIMEOUT APP_TIMER_TICKS(1000 * 60 * 5) //turn off bluetooth after 5 min

void shutdown(void);

uint16_t cnt_1;

void antplus_controls_evt_handler(antplus_controls_profile_t *p_profile, antplus_controls_evt_t event)
{
  nrf_pwr_mgmt_feed();

  switch (event)
  {
  case ANTPLUS_CONTROLS_PAGE_73_UPDATED:
    break;

  default:
    break;
  }
}

void ant_lev_evt_handler(ant_lev_profile_t *p_profile, ant_lev_evt_t event)
{
  nrf_pwr_mgmt_feed();
  // get motor state variables
  motor_init_state = p_profile->common.gear_state & 0x03;
  motor_error_state = (p_profile->common.gear_state) >> 2;

  switch (event)
  {
  case ANT_LEV_PAGE_1_UPDATED:
      //  p_profile->page_16.travel_mode = p_profile->common.travel_mode_state;
      ;
    break;

  case ANT_LEV_PAGE_2_UPDATED:
    break;

  case ANT_LEV_PAGE_3_UPDATED:
    motor_soc_state = round(p_profile->page_3.battery_soc / 10); //0 to 10
    break;

  case ANT_LEV_PAGE_4_UPDATED:
    break;

  case ANT_LEV_PAGE_5_UPDATED:
    break;

  case ANT_LEV_PAGE_34_UPDATED:

    break;

  case ANT_LEV_PAGE_16_UPDATED:

    break;

  case ANT_LEV_PAGE_80_UPDATED:

    break;

  case ANT_LEV_PAGE_81_UPDATED:

    break;

  case ANT_LEV_PAGE_REQUEST_SUCCESS:

    break;

  case ANT_LEV_PAGE_REQUEST_FAILED:
    break;

  default:
    break;
  }
}

void wait_and_reset(void)
{
  nrf_lp_delay_ms(WAIT_TIME);
  sd_nvic_SystemReset(); // reset and start again
}
void ANT_Search_Stop(void) //ant search has timed out without finding a device
{
  ret_code_t err_code;
  err_code = app_timer_stop(ANT_Search_timer);
  APP_ERROR_CHECK(err_code);
  searching_flag = false;
}
void ANT_Search_Start(void)
{
  ret_code_t err_code;
  err_code = app_timer_start(ANT_Search_timer, ANT_Search_TIMEOUT, NULL);
  searching_flag = true;
  APP_ERROR_CHECK(err_code);
}
static void ANT_Search_timeout(void *p_context) //check every 400 ms
{
  UNUSED_PARAMETER(p_context);
  // first see if ANT pairing is completed
  uint8_t LEV_Status;
  uint8_t CTRL_Status;
  ret_code_t err_code;
  static uint8_t ui8_cnt_ant_search_timeout = 0;

  // keep a counter for the number of ANT search timeouts
  ui8_cnt_ant_search_timeout++;
  if (ui8_cnt_ant_search_timeout > 50) // 600ms * 50 = 30 seconds
  {
    // if is not connected, shutdown
    shutdown_flag = true;
    return;
  }
  if (searching_flag)
    led_sequence_play(LED_EVENT_ANT_DISCONNECT);
  err_code = sd_ant_channel_status_get(LEV_CHANNEL_NUM, &LEV_Status);
  APP_ERROR_CHECK(err_code);
  err_code = sd_ant_channel_status_get(CONTROLS_CHANNEL_NUM, &CTRL_Status);
  APP_ERROR_CHECK(err_code);

  if (ebike && garmin) //both ant profiles are active
  {
    if (LEV_Status != (uint8_t)STATUS_SEARCHING_CHANNEL && CTRL_Status != (uint8_t)STATUS_SEARCHING_CHANNEL) // both device are paired
    {
      APP_ERROR_CHECK(err_code);
      ui8_cnt_ant_search_timeout = 0;
      err_code = app_timer_stop(ANT_Search_timer);
      APP_ERROR_CHECK(err_code);

      led_sequence_play_next(LED_EVENT_ANT_CONNECT);

      searching_flag = false;
    }

    return;
  }

  if (ebike)
  {
    if (LEV_Status != (uint8_t)STATUS_SEARCHING_CHANNEL)
    {

      ui8_cnt_ant_search_timeout = 0;
      led_sequence_play_next(LED_EVENT_ANT_CONNECT);
      err_code = app_timer_stop(ANT_Search_timer);

      searching_flag = false;
    }
    return;
  }
  if (garmin)
  {
    if (CTRL_Status != (uint8_t)STATUS_SEARCHING_CHANNEL)
    {
      ui8_cnt_ant_search_timeout = 0;

      led_sequence_play_next(LED_EVENT_ANT_CONNECT);
      err_code = app_timer_stop(ANT_Search_timer);

      searching_flag = false;
    }
    return;
  }
}

static void bluetooth_timer_timeout(void *p_context)
{
  UNUSED_PARAMETER(p_context);
  disable_configuration = true;
}
static void timer_button_config_press_timeout_handler(void *p_context)
{
  UNUSED_PARAMETER(p_context);

  config_press = true;
  // enter configuration mode
  if (configuration_flag)
  {
    disable_configuration = true;
    enable_configuration = false;
  }
  else
  {
    enable_configuration = true;
    disable_configuration = false;
  }
}
static void timer_button_press_timeout_handler(void *p_context)
{
  UNUSED_PARAMETER(p_context);

  // enter ultra low power mode
  shutdown_flag = true;
}
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
int main(void)
{
  ret_code_t err_code;
  //lfclk_config()
  ram_retention_setup();
  sd_power_dcdc_mode_set(NRF_POWER_DCDC_ENABLE);
  softdevice_setup();

  leds_init();

  init_app_timers();
  buttons_init();
  led_init(); //pwm initialization
  led_sequence_play(LED_EVENT_WIRELESS_BOARD_POWER_ON);
  //read the flash memory and setup the ANT ID and Bluetooth flag
  eeprom_init(&old_ant_device_id, &configuration_flag, &ebike, &garmin, &brake);
  new_ant_device_id = old_ant_device_id; //no change at this time.
  
  if (configuration_flag)
  {
    led_sequence_play_next(LED_EVENT_CONFIGURATION_MODE);

    //start the bluetooth 5 min timer -turn off configurartion mode automatically in 5 minutes
    err_code = app_timer_start(bluetooth_timer, BLUETOOTH_TIMEOUT, NULL);
    APP_ERROR_CHECK(err_code);
    ble_init();
  }
  else
  {
    profile_setup();
  }

  power_mgt_init();

  //idle loop
  while (true)
  {
    nrf_pwr_mgmt_run();
    check_interrupt_flags();
  }
}

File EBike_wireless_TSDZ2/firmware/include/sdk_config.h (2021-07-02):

/**
 * Copyright (c) 2017 - 2019, Nordic Semiconductor ASA
 *
 * All rights reserved.
 *
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
 * 3. Neither the name of Nordic Semiconductor ASA nor the names of its
 *    contributors may be used to endorse or promote products derived from this
 *    software without specific prior written permission.
 *
 * 4. This software, with or without modification, must only be used with a
 *    Nordic Semiconductor ASA integrated circuit.
 *
 * 5. Any software provided in binary form under this license must not be reverse
 *    engineered, decompiled, modified and/or disassembled.
 *
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
 */

#ifndef SDK_CONFIG_H
#define SDK_CONFIG_H
// <<< Use Configuration Wizard in Context Menu >>>\n
#ifdef USE_APP_CONFIG
#include "app_config.h"
#endif

// <e> NRF_CLOCK_ENABLED - nrf_drv_clock - CLOCK peripheral driver - legacy layer
//==========================================================
#ifndef NRF_CLOCK_ENABLED
#define NRF_CLOCK_ENABLED 1
#endif
// <o> CLOCK_CONFIG_LF_SRC  - LF Clock Source
 
// <0=> RC 
// <1=> XTAL 
// <2=> Synth 
// <131073=> External Low Swing 
// <196609=> External Full Swing 

#ifndef CLOCK_CONFIG_LF_SRC
#define CLOCK_CONFIG_LF_SRC 1
#endif

// <q> CLOCK_CONFIG_LF_CAL_ENABLED  - Calibration enable for LF Clock Source
 

#ifndef CLOCK_CONFIG_LF_CAL_ENABLED
#define CLOCK_CONFIG_LF_CAL_ENABLED 0
#endif

// <o> CLOCK_CONFIG_IRQ_PRIORITY  - Interrupt priority
 

// <i> Priorities 0,2 (nRF51) and 0,1,4,5 (nRF52) are reserved for SoftDevice
// <0=> 0 (highest) 
// <1=> 1 
// <2=> 2 
// <3=> 3 
// <4=> 4 
// <5=> 5 
// <6=> 6 
// <7=> 7 

#ifndef CLOCK_CONFIG_IRQ_PRIORITY
#define CLOCK_CONFIG_IRQ_PRIORITY 6
#endif

// </e>

// <e> NRFX_CLOCK_ENABLED - nrfx_clock - CLOCK peripheral driver
//==========================================================
#ifndef NRFX_CLOCK_ENABLED
#define NRFX_CLOCK_ENABLED 1
#endif
// <o> NRFX_CLOCK_CONFIG_LF_SRC  - LF Clock Source
 
// <0=> RC 
// <1=> XTAL 
// <2=> Synth 
// <131073=> External Low Swing 
// <196609=> External Full Swing 

#ifndef NRFX_CLOCK_CONFIG_LF_SRC
#define NRFX_CLOCK_CONFIG_LF_SRC 1
#endif

// <o> NRFX_CLOCK_CONFIG_IRQ_PRIORITY  - Interrupt priority
 
// <0=> 0 (highest) 
// <1=> 1 
// <2=> 2 
// <3=> 3 
// <4=> 4 
// <5=> 5 
// <6=> 6 
// <7=> 7 

#ifndef NRFX_CLOCK_CONFIG_IRQ_PRIORITY
#define NRFX_CLOCK_CONFIG_IRQ_PRIORITY 6
#endif

// <e> NRFX_CLOCK_CONFIG_LOG_ENABLED - Enables logging in the module.
//==========================================================
#ifndef NRFX_CLOCK_CONFIG_LOG_ENABLED
#define NRFX_CLOCK_CONFIG_LOG_ENABLED 0
#endif
// <o> NRFX_CLOCK_CONFIG_LOG_LEVEL  - Default Severity level
 
// <0=> Off 
// <1=> Error 
// <2=> Warning 
// <3=> Info 
// <4=> Debug 

#ifndef NRFX_CLOCK_CONFIG_LOG_LEVEL
#define NRFX_CLOCK_CONFIG_LOG_LEVEL 3
#endif

// <o> NRFX_CLOCK_CONFIG_INFO_COLOR  - ANSI escape code prefix.
 
// <0=> Default 
// <1=> Black 
// <2=> Red 
// <3=> Green 
// <4=> Yellow 
// <5=> Blue 
// <6=> Magenta 
// <7=> Cyan 
// <8=> White 

#ifndef NRFX_CLOCK_CONFIG_INFO_COLOR
#define NRFX_CLOCK_CONFIG_INFO_COLOR 0
#endif

// <o> NRFX_CLOCK_CONFIG_DEBUG_COLOR  - ANSI escape code prefix.
 
// <0=> Default 
// <1=> Black 
// <2=> Red 
// <3=> Green 
// <4=> Yellow 
// <5=> Blue 
// <6=> Magenta 
// <7=> Cyan 
// <8=> White 

#ifndef NRFX_CLOCK_CONFIG_DEBUG_COLOR
#define NRFX_CLOCK_CONFIG_DEBUG_COLOR 0
#endif

// </e>

// </e>

// <e> NRFX_UARTE_ENABLED - nrfx_uarte - UARTE peripheral driver
//==========================================================
#ifndef NRFX_UARTE_ENABLED
#define NRFX_UARTE_ENABLED 1
#endif
// <o> NRFX_UARTE0_ENABLED - Enable UARTE0 instance 
#ifndef NRFX_UARTE0_ENABLED
#define NRFX_UARTE0_ENABLED 0
#endif

// <o> NRFX_UARTE_DEFAULT_CONFIG_HWFC  - Hardware Flow Control
 
// <0=> Disabled 
// <1=> Enabled 

#ifndef NRFX_UARTE_DEFAULT_CONFIG_HWFC
#define NRFX_UARTE_DEFAULT_CONFIG_HWFC 0
#endif

// <o> NRFX_UARTE_DEFAULT_CONFIG_PARITY  - Parity
 
// <0=> Excluded 
// <14=> Included 

#ifndef NRFX_UARTE_DEFAULT_CONFIG_PARITY
#define NRFX_UARTE_DEFAULT_CONFIG_PARITY 0
#endif

// <o> NRFX_UARTE_DEFAULT_CONFIG_BAUDRATE  - Default Baudrate
 
// <323584=> 1200 baud 
// <643072=> 2400 baud 
// <1290240=> 4800 baud 
// <2576384=> 9600 baud 
// <3862528=> 14400 baud 
// <5152768=> 19200 baud 
// <7716864=> 28800 baud 
// <8388608=> 31250 baud 
// <10289152=> 38400 baud 
// <15007744=> 56000 baud 
// <15400960=> 57600 baud 
// <20615168=> 76800 baud 
// <30801920=> 115200 baud 
// <61865984=> 230400 baud 
// <67108864=> 250000 baud 
// <121634816=> 460800 baud 
// <251658240=> 921600 baud 
// <268435456=> 1000000 baud 

#ifndef NRFX_UARTE_DEFAULT_CONFIG_BAUDRATE
#define NRFX_UARTE_DEFAULT_CONFIG_BAUDRATE 30801920
#endif

// <o> NRFX_UARTE_DEFAULT_CONFIG_IRQ_PRIORITY  - Interrupt priority
 
// <0=> 0 (highest) 
// <1=> 1 
// <2=> 2 
// <3=> 3 
// <4=> 4 
// <5=> 5 
// <6=> 6 
// <7=> 7 

#ifndef NRFX_UARTE_DEFAULT_CONFIG_IRQ_PRIORITY
#define NRFX_UARTE_DEFAULT_CONFIG_IRQ_PRIORITY 6
#endif
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

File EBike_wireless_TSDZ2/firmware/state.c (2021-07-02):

/*
 * Bafang LCD 850C firmware
 *
 * Copyright (C) Casainho, 2018.
 *
 * Released under the GPL License, Version 3
 */

#include <math.h>
#include <stdlib.h>
#include "stdio.h"
#include "uart.h"
#include "utils.h"
#include "state.h"
#include "ledalert.h"

typedef enum {
  FRAME_TYPE_ALIVE = 0,
  FRAME_TYPE_STATUS = 1,
  FRAME_TYPE_PERIODIC = 2,
  FRAME_TYPE_CONFIGURATIONS = 3,
  FRAME_TYPE_FIRMWARE_VERSION = 4,
} frame_type_t;

static uint8_t ui8_m_usart1_received_first_package = 0;
uint8_t ui8_g_battery_soc;

volatile uint8_t m_get_tsdz2_firmware_version; // true if we are simulating a motor (and therefore not talking on serial at all)
volatile motor_init_state_t g_motor_init_state = MOTOR_INIT_OFF;
volatile motor_init_state_config_t g_motor_init_state_conf = MOTOR_INIT_CONFIG_SEND_CONFIG;
volatile motor_init_status_t ui8_g_motor_init_status = MOTOR_INIT_STATUS_RESET;

tsdz2_firmware_version_t g_tsdz2_firmware_version = { 0xff, 0, 0 };

rt_vars_t rt_vars;
ui_vars_t ui_vars;

volatile bool m_reset_wh_flag = false;

// Set to true if we should automatically convert kph -> mph and km -> mi
bool screenConvertMiles = false;

// Set to true if we should automatically convert C -> F
bool screenConvertFarenheit = false;

// Set to true if we should automatically convert kg -> lb
bool screenConvertPounds = false;

extern void rt_processing_stop(void);
extern void rt_processing_start(void);

ui_vars_t* get_ui_vars(void) {
	return &ui_vars;
}

rt_vars_t* get_rt_vars(void) {
  return &rt_vars;
}

void set_conversions(void) {
  screenConvertMiles = ui_vars.ui8_units_type != 0; // Set initial value on unit conversions (FIXME, move this someplace better)
  screenConvertFarenheit = screenConvertMiles; // FIXME, should be based on a different eeprom config value
  screenConvertPounds = screenConvertMiles;
}

void rt_send_tx_package(frame_type_t type) {
  uint8_t crc_len = 3; // minimun is 3
	uint8_t *ui8_usart1_tx_buffer = uart_get_tx_buffer();

	/************************************************************************************************/
	// send tx package
	// start up byte
	ui8_usart1_tx_buffer[0] = 0x59;
  ui8_usart1_tx_buffer[1] = crc_len;
  // type of the frame
	ui8_usart1_tx_buffer[2] = (uint8_t) type;

	switch (type) {
	  case FRAME_TYPE_PERIODIC:
      if (rt_vars.ui8_walk_assist) {
        ui8_usart1_tx_buffer[3] = (uint8_t) rt_vars.ui8_walk_assist_level_factor[((rt_vars.ui8_assist_level) - 1)];
        ui8_usart1_tx_buffer[4] = 0;
      } else if (rt_vars.ui8_assist_level) {
        uint16_t ui16_temp = rt_vars.ui16_assist_level_factor[((rt_vars.ui8_assist_level) - 1)];
        ui8_usart1_tx_buffer[3] = (uint8_t) (ui16_temp & 0xff);
        ui8_usart1_tx_buffer[4] = (uint8_t) (ui16_temp >> 8);
      } else {
        // if rt_vars.ui8_assist_level = 0, send 0!! always disable motor when assist level is 0
        ui8_usart1_tx_buffer[3] = 0;
        ui8_usart1_tx_buffer[4] = 0;
      }

      ui8_usart1_tx_buffer[5] = (rt_vars.ui8_lights & 1) | ((rt_vars.ui8_walk_assist & 1) << 1);

      // battery power limit
      if (rt_vars.ui8_street_mode_enabled)
      {
        ui8_usart1_tx_buffer[6] = rt_vars.ui8_street_mode_power_limit_div25;
      }
      else
      {
        ui8_usart1_tx_buffer[6] = rt_vars.ui8_target_max_battery_power_div25;
      }

      // startup motor power boost
      uint16_t ui16_temp = (uint8_t) rt_vars.ui16_startup_motor_power_boost_factor[((rt_vars.ui8_assist_level) - 1)];
      ui8_usart1_tx_buffer[7] = (uint8_t) (ui16_temp & 0xff);
      ui8_usart1_tx_buffer[8] = (uint8_t) (ui16_temp >> 8);

      // wheel max speed
      if (rt_vars.ui8_street_mode_enabled)
      {
        ui8_usart1_tx_buffer[9] = rt_vars.ui8_street_mode_speed_limit;
      }
      else
      {
        ui8_usart1_tx_buffer[9] = rt_vars.ui8_wheel_max_speed;
      }

      // motor temperature limit function or throttle
      if (rt_vars.ui8_street_mode_enabled &&
          rt_vars.ui8_street_mode_throttle_enabled)
      {
        ui8_usart1_tx_buffer[10] = rt_vars.ui8_temperature_limit_feature_enabled & 1;
      }
      else
      {
        ui8_usart1_tx_buffer[10] = rt_vars.ui8_temperature_limit_feature_enabled & 3;
      }

      // virtual throttle
      ui8_usart1_tx_buffer[11] = (uint8_t) ((((uint16_t) rt_vars.ui8_throttle_virtual) * 255) / 100);

      crc_len = 13;
      ui8_usart1_tx_buffer[1] = crc_len;
	    break;

    // set configurations
	  case FRAME_TYPE_CONFIGURATIONS:
      // battery low voltage cut-off
      ui8_usart1_tx_buffer[3] = (uint8_t) (rt_vars.ui16_battery_low_voltage_cut_off_x10 & 0xff);
      ui8_usart1_tx_buffer[4] = (uint8_t) (rt_vars.ui16_battery_low_voltage_cut_off_x10 >> 8);

      // wheel perimeter
      ui8_usart1_tx_buffer[5] = (uint8_t) (rt_vars.ui16_wheel_perimeter & 0xff);
      ui8_usart1_tx_buffer[6] = (uint8_t) (rt_vars.ui16_wheel_perimeter >> 8);

      // battery max current
      ui8_usart1_tx_buffer[7] = rt_vars.ui8_battery_max_current;

      ui8_usart1_tx_buffer[8] = rt_vars.ui8_startup_motor_power_boost_feature_enabled |
          (rt_vars.ui8_startup_motor_power_boost_always << 1) |
          (rt_vars.ui8_startup_motor_power_boost_limit_power << 2) |
          (rt_vars.ui8_torque_sensor_calibration_feature_enabled << 3) |
          (rt_vars.ui8_torque_sensor_calibration_pedal_ground << 4) |
          (rt_vars.ui8_motor_assistance_startup_without_pedal_rotation << 5) |
          ((rt_vars.ui8_motor_type & 1) << 6);

      // motor max current
      ui8_usart1_tx_buffer[9] = rt_vars.ui8_motor_max_current;
      // startup motor power boost time
      ui8_usart1_tx_buffer[10] = rt_vars.ui8_startup_motor_power_boost_time;
      // startup motor power boost fade time
      ui8_usart1_tx_buffer[11] = rt_vars.ui8_startup_motor_power_boost_fade_time;

      // motor over temperature min and max values to limit
      ui8_usart1_tx_buffer[12] = rt_vars.ui8_motor_temperature_min_value_to_limit;
      ui8_usart1_tx_buffer[13] = rt_vars.ui8_motor_temperature_max_value_to_limit;

      ui8_usart1_tx_buffer[14] = rt_vars.ui8_ramp_up_amps_per_second_x10;

      // TODO
      // target speed for cruise
      ui8_usart1_tx_buffer[15] = 0;
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

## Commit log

2020-05-30 ANT+ and BLE heart rate example works
    [nrf52.cfg, stlink-v2.cfg]
2020-06-03 HR tx and rx, sensor and display, example, builds and should work
2020-06-18 Added documentation and schematic folders
2020-06-18 Add files via upload
    Wiring schematic and supporting datasheets.
2020-06-24 Add files via upload
    Updated with extra comments, simplification and optional components
    [Wireless_eBike_V1.sch]
2020-06-30 Organization of project files. Simple main.c file builds and debugs. Added configuration files for Code Studio to flash and debug
    [nrf52.cfg, stlink-v2.cfg]
2020-07-05 Couple minor changes to development documentation
2020-07-10 Added control of motor power, in this case, just for testing, when asssit level == 0, motor off and asssit level > 0, motor on
2020-07-10 Updated schematic
    [Wireless_eBike.sch, Wireless_eBike_V1.sch]
2020-07-12 Add in MDK pin configuration and switch for pca10059
2020-07-25 Updated schematic and moved all schematic images into schematic folder.
    [Wireless_eBike-2020-07-10-23-53-44.sch, Wireless_eBike_V1-2020-07-10-22-59-47.sch, Wireless_eBike_V1-2020-07-10-23-00-45.sch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]
2020-09-11 fixes type nRF5280 → nRF52840
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2020-09-17 UART and EEPROM code seems to build
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2020-10-01 Code builds for UART tx and rx, motor init. Not tested
2020-10-07 TSDZ2 wireless EBike ANT+ LEV works, although very limited with working only the changing assist level
2020-12-08 Communications works with mobile app v0.1.0
    [nrf52.cfg, stlink-v2.cfg]
2020-12-08 For some reason, the Bluetooth communication did not work after the clen up...
    Revert "main.c clean, moved Bluetooth code ble_project.c"
    This reverts commit 354b41f6300db4a2ed578e0d3766ffedac82b5d5.
    [eeprom.c, main.c]
2020-12-08 Corrected issue where FDS init would fail: openocd now fully erases the memory and that is the solution. Openocd need to be updated to latest develop version to support the nrf5 mass_erase command
    [sdk_config.h]
2020-12-29 Added TSDZ2 motor init. Added brake and lights status to Bluetooth
2021-01-05 Improved motor startup state. Works for mobile app v0.2.0
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2021-01-16 updated schematic based on latest prototypes
    [Wireless_eBike-2020-07-10-23-53-44.sch, Wireless_eBike.sch, Wireless_eBike_V1-2020-07-10-22-59-47.sch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]
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2021-01-19 Added bootloader, remote and wireless board firmwares all on this repository and they share common files like the Nordic SDK. The idea in future is the share code between the projects as the have com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
    [Battery_Life_Calculator.xls, VLCD5.stl, VLCD5_2.FCStd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]
2021-01-21 get firmware working in new repository
    [nrf52.cfg, stlink-v2.cfg, stlink.cfg]
2021-01-21 fix ant speed, battery charge, and voltage
    [main.c]
2021-01-22 Updated schematics
    [Wireless_eBike.sch, ebike_remote_wireless.sch]
2021-01-23 Added schematic for bootloader
    [Ebike_wireless_bootloader.sch]
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2021-01-23 led fix
2021-01-23 I forgot to release the brake flag on the motor!
2021-01-23 Updated schematic for the TSDZ2 wireless board and remote, removing the bootloader flash
    [Wireless_eBike.sch, ebike_remote_wireless.sch]
2021-01-23 fix brake led duration
    [main.c]
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2021-01-24 Updated brake pin
    [ebike_remote_wireless.sch]
2021-01-26 Removed nrf52840_mdk_usb_dongle usage on EBike_wireless_remote. Updated wireless board schematic to correct small bug on GND connection
    [Wireless_eBike.sch]
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2021-01-28 fix long press flash
    [main.c]
2021-01-30 fixed missing assist commands
    [main.c]
2021-02-01 Fix LED signalling
2021-02-02 Added brake support to the TSDZ2 wireless board
2021-02-02 v0.0.6. Also inverted Garmin page rotation
    [main.c]
2021-02-02 fix leds signalling
2021-02-02 fix enter key paging
    [main.c]
2021-02-04 Revert "working"
    This reverts commit eb581a3a67ad9bb4bbc12fb9a767e30a71865944.
    [buttons.c, main.c, pins.c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]
2021-02-05 configuration mode bug fix
    [main.c]
2021-02-06 fix leds wip
2021-02-07 Update main.c
    Uses method similar to motor controller - using ms counter not ticks
2021-02-07 correct button constant
2021-02-07 Update buttons.c
    Buttons now need to be pressed for at least one cycle (50ms) - to filter out random noise presses.
    [buttons.c]
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2021-02-12 pwm updates
    general tidying - moving things out of header files that don't need to be there
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2021-02-13 Update ledalert.c
    correct typo
    [ledalert.c]
2021-02-13 Updates to ledalerts
    Fix typo in led_clear_queue
    Reduce lowest brightness level power consumption
    Add additional brightness levels
    Enable global brightness setting
    Add led events for battery soc
    Add soc display at power off
    Make leds brighter on wireless controller
    Make leds dim when lights are on and vice versa.
    [ledalert.c, ledalert.h, main.c]
2021-02-13 Update main.c
    Make assist changes on the app raise led events on the wireless controller
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2021-02-13 Revert "leds active on app assist up/down"
    This reverts commit 09a563f598d59ea2566de694da63405b4f4ac54b.
    [ledalert.h, main.c]
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2021-02-16 fix button debounce
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2021-02-18 Update ledalert.c
    more power improvements - hopefully should improve power utilisation when led is on - and show differences in power utilisation between brightness levels
2021-02-18 Update ledalert.c
    trying to make it sleep after led sequence
2021-02-18 Revert "Update ledalert.c"
    This reverts commit 0e9ddb308727e2db3fd79dd2e7c9e492e3da3cff.
    [ledalert.c]
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2021-02-19 release candidate
    [Battery_Life_Calculator.xls]
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2021-02-20 Revert "wired remote release"
    This reverts commit 87bd76cc03925592a5a26182a691f3b6b342096a.
    [ledalert.c, ledalert.h, main.c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]
2021-02-21 Wired Remote Schematic v0.1
    [Wired_remote.sch]
2021-02-21 new led alert functions
    [Battery_Life_Calculator.xls]
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2021-02-22 fds flash bug fix
    [eeprom.c, main.c]
2021-02-22 fix leds
2021-02-23 flash garbage collection fix
    [eeprom.c]
2021-02-23 led signalling changes and flash bug fix
    [main.c]
2021-02-24 Update ledalert.c
    Change to make sure that sequences queued aren't lost - is a bit of a hack - will work on a better solution.
2021-02-24 fix led sequencing
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2021-02-26 led alert updates
    Remove last legacy calls in header
    Remove hackage to work around issue if play_next called to often in succession
    [ledalert.c, ledalert.h]
2021-03-01 Big update to the wireless remote 3D print enclosure
    [VLCD5.stl, VLCD5_2.FCStd, VLCD5_LowerPart.FCStd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]
2021-03-02 Remote 3D design: small update to lower part
    [assembly.FCStd, crc2032.FCStd, lower_part.FCStd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]
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2021-03-03 Update to wireless remote 3D print files
    [assembly.FCStd, keypad.FCStd, keypad.stl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]
2021-03-03 fix brake brightess,on/off flash
    [ledalert.h, main.c]
2021-03-03 FIX BUTTON DEFINITIONS
2021-03-05 Wireless remote: updated 3D files
    [CRC2032.FCStd, assembly.FCStd, clamp.FCStd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]
2021-03-05 Wireless remote: moved STL files to 3D_print folder
    [clamp.stl, keypad.stl, lower_part.stl]
2021-03-28 add brake LED signal, clean up old code
2021-04-08 power loop fix
2021-04-18 Added 3D design files for TSDZ2-wireless-box. Updated the 3D print files of wireless remote, as there was an issue with holes of the 3D printed files
    [CRC2032.FCStd, TSDZ2-wireless-box.FCStd, TSDZ2-wireless-box.amf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]
2021-04-24 Updated the wired remote page, to export a PNG image without showing the details of page author, etc
    [Battery_Life_Calculator.xls, CRC2032.FCStd, Ebike_wireless_bootloader.sch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]
2021-04-30 Added screws to the assembly. Updated the lower and keypad parts for correct screw size
    [CRC2032.FCStd, assembly.FCStd, keypad.FCStd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]
2021-05-10 Correction to issue where the wireless remote firmware would block after the no keypress timeout
    [main.c]
2021-05-10 Added 3D design files for TSDZ2 wireless controller small box
    [CRC2032.FCStd, TSDZ2-wireless-box.FCStd, TSDZ2-wireless-box.amf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]
2021-05-14 Added design files for box
    [TSDZ2_wireless_box.FCStd, TSDZ2_wireless_box.amf, TSDZ2_wireless_box_cover.FCStd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]
2021-05-30 Battery SOC now resets everytime the voltage is over the configured limit
    [eeprom.c, state.c]
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2021-07-25 Removed button hole from TSDZ2 wireless small box cover, as it is now possible to press the button without the hole
    [TSDZ2_wireless_small_box_cover.FCStd, TSDZ2_wireless_small_box_cover.amf]
2021-08-10 Added JLink flash and debug scripts. Added new version of 3D files for both wireless controller as also wireless remote
    [CRC2032.FCStd, EBike_wireless_remote.FCStd, EBike_wireless_remote.amf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]
